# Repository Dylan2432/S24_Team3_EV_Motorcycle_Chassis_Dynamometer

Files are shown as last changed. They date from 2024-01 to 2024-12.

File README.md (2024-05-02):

# Electric Motorcycle Test Station

## Executive Summary

Proton Power is developing a cutting-edge battery to revolutionize electric motorcycles, addressing challenges in charging and range. Our team's project is to integrate a data acquisition system (DAQ) into a chassis dynamometer for crucial testing, ensuring accurate data collection and product validation. By selecting and integrating sensors meticulously, we aim to deliver a motorcycle test station with optimal performance while adhering to safety standards and engineering ethics.

## Capabilities

This dynamometer is designed to test and measure the performance metrics of an electric motorcycle. It shall have the following capabilities:
1. Fully remote-operable from PC 
2. Plot bike speed and torque in real time on PC
3. Data logging for later analysis
4. Support bike speeds of 0-75km/hr
5. Support incline testing for 0-8% road grade
6. Adjust bike speed in 1km/hr increments
8. Able to be disassembled for transport
9. Emergency stop capable

## Salient Outcomes

To be updated as the project progresses

## Project Demonstration & Images

Project demos and images will be uploaded as the project progresses.

## About Us

### Team

**Ethan Griffith** is a senior Electrical Engineering major at Tennessee Technological University with a minor in Mathematics. Ethan has an interest in wireless power transfer and mechatronics. For this project, Ethan focused on the design of the remote throttle control system. 

**Andrew Copeland** is a senior Electrical Engineering major at Tennessee Tech. His interests include power systems, control systems, and mechatronics. Andrew's role in this project is the design and implementation of a user interface for the test system.

**Aaron Littleton** is a senior Electrical Engineering major at Tennessee Tech with a minor in Mathematics. Aaron's interests include power systems and power grid design.  His role in this project is the design and implementation of the data acquisition system.   

**Dylan Scruggs** is a senior Electrical Engineering major at Tennessee Tech. Dylan has interests in power systems and mechatronics. His role in this project is the design and implementation of the controlled braking system.

**Jonathan Haas** is a senior majoring in Electrical Engineering and Business Management. Jonathan's interests are in critical power systems and power management. His role in this project is the design, implementation, and testing of sensors for the dynamometer.

**Branson Stephens** is a senior Elecitrical Engineering major at Tennessee Tech. Branson's interests are in PLC programming and Telecommunications. His role in the project is the design and implementation of a variable power supply to support the braking system that is controlled from the user interface.

### Faculty Supervisor

**Jesse Roberts**, M.S. is a lecturer at Tennessee Technological University. He received both his Bachelor's and Master's in Electrical Engineering at Tennessee Technological University. He is currently pursuing a Doctorate of Philosophy in Computer Science at Vanderbilt University.

### Stakeholders

The main stakeholder in this project is our customer Proton Power. Proton Power is a pioneering force in the realm of efficient energy, striving to overcome the global challenge of diverse charging requirements. Their cutting-edge battery technology promises faster charging and extended range, that will revolutionize the EV landscape. Proton Power is leading the design of an EV motorcycle battery with an impressive range of 400km on a single charge, offered at a fraction of the cost compared to existing models. We plan to aid them in this mission but providing data that will allow them to innovate their technology even further.

Another stakeholder in the project is Bob. Bob is a leading manufacturer specializing in electric vehicles (EVs), particularly focusing on providing affordable transportation solutions for third-world countries. With a mission to address the financial burdens associated with traditional gas-driven motorcycles, Bob has shifted its focus to producing EV bikes with lower maintenance and fuel costs. With the addition of the advanced battery from Proton along with the testing done by this team, Bob can greatly improve upon this mission.

### Recognitions

We would like to thank Jesse Roberts for continually giving feedback and advice on the project and investing plenty of time and effort into the project. We would also like to thank our mechanical engineering partnering team for providing useful insight from a unique perspective and helping the team with any mechanical problems. Next, we would like to thank past Capstone teams for their advice and support. Last but not least, we would like to thank Proton Power for giving us the opportunity to apply the knowledge learned in class to the bike they have provided us to test on.  

## Repo Organization

### [Reports](/Reports)

In the reports section of this repository information about the individual expectations for the reports and how they should be housed is provided.

The [**Project Proposal**](./Reports/Project%20Proposal/Project_Proposal_V2.pdf): Is the intial document that defines the problem and the goals of the project.

The [**Conceptual Design**](./Reports/Conceptual%20Design/Conceptual%20Design%20and%20Planning.pdf): Gives a deeper breakdown of what the problem is, a breakdown of the subsystems of the project, and a projected timeline and budget of the project.  

### [Documentation](/Documentation)

Contains:

[**Meeting Minutes**](/Documentation/Meeting%20Minutes) : typed meeting minutes from team meetings which occured weekly at the minimum

[**Signoffs**](/Documentation/Signoffs): reports for each approved subsystem containing functionality, constraints, schematics, analysis, and BOM

### [Software](./Software)

All software utilized for the project can be found in the this folder.

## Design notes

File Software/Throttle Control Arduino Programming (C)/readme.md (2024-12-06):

Must have Arduino IDE downloaded in order to open file

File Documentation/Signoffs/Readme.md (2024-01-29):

## How to submit a signoff or update a signoff:

### Submitting Signoff
1. Create the signoff markdown file 
2. At the bottom of the page select "create a new branch for this commit and start a pull request"
3. Submit the changes 
4. Name the pull request branch "name-signoff-subsystem name"
5. The comment should be "requesting signoff for name of subsystem"
6. Submit the pull request
7. Wait for faculty supervisor feedback on the pull request

### Updating Signoff

1. Edit the signoff markdown file 
2. Add a description of how you have addressed the feedback from the faculty supervisor
3. At the bottom of the page select "commit directly to"
4. Submit the changes 

# Required sections

Each signoff markdown file must contain the following sections and information:

## Function of the Subsystem

You must explain clearly what role the subsystem will play in the first section. This should clearly explain what the system is expected to do (ie. its atomic purpose from the conceptual design).

## Constraints

The second section should contain the constraints for the subsystem. The reasoning behind the constraints must be given. As a few examples, constraints may exist due to physics based limitations or requirements, other subsystem requirements, standards, ethics, or socioeconomic reasons. 

Each subsystem must have at least one constraint arising from standards, ethics, or socioeconomic well being.

## Buildable schematic 

The third section should show the buildable schematic directly embedded in the markdown file as a jpeg image. If the schematic is not clearly readable and appropriately sized, the supervisor will reject the signoff. 

The schematic must be appropriate to the design. ie. 3d model for a physical system or wiring schematic for a circuit. Further, the schematic(s) must contain every detail necessary for the design to be built by someone who has no knowledge of the design. Every relevant component value and measurement must be given.

The actual design artifacts (3d model, Cad files, gerber files, etc) must be uploaded to the documentation folder in the appropriate location.

## Analysis

A complete and relevant analysis of the design showing that it **should** meet the constraints and perform the desired function must be given. This analysis must be comprehensive and well explained so that it is convincing to the faculty supervisor. If the signoff request is not convincing either because the requirements and constraints are insufficient, unjustified, or not appropriately shown to be met by the design, then approval will not be given. Without approval, the components for the subsystem aren't allowed to be ordered. 

## BOM

A complete list of all components needed for the design must be given with the cost of each component and the total cost of the subsystem. The BOM should be a markdown table.

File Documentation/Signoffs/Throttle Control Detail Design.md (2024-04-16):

# Throttle Control Subsystem

## Functionality
The purpose of the Remote Throttle Control Subsystem is to be able to adjust the speed of the EV bike while it is on the dyno without having to be near the bike and adjust it manually. It allows the adjustments of the speed to be made based on the input of the user and be able to set test runs to change to multiple speeds within a single test run. This is done for safety concerns so that there does not have to be a user on the bike while it is running on the dyno and instead can be operated from a safe distance.

## Constraints
| No. | Constraints | Origin |
|-----|---|---|
| 1 | Be able to rotate the entire range of the throttle on the bike by a signal from a controller. | Safety Constraint |
| 2 | Support repeatedly testing the bike from 0 km/h to 50 km/h and then back down to 0 km/h. | Design Constraint |
| 3 | Be able to adjust operating speeds in 1 km/h increments and measure response time. | Design Constraint |
| 4 | Be able to adjust the throttle from a dead stop to a full throttle in under 200ms. | Design Constraint |

1. This constraint is set into place to keep all personnel operating the equipment and testing the bike safe. By allowing it to be operated remotely, all testing can be done at a safe distance, so no one will be injured in case something were to go wrong. It also serves as a way to increase the accuracy of testing by not having to worry about the weight of someone on the bike while it is running and being able to precisely change the speed at desired increments. 

2. This is a specification that was made by the customer. According to this, test runs must be incorporated into the programming for the user interface so that the user can create set runs to allow the bike to go through without having to change it every time. For example, the user should be able to select a test run through the user interface that will make the bike go from 0 km/h to 50 km/h and then back to 0 km/h, and the bike will perform this run without having to manually enter in each step every time. This will make the testing procedures much more convenient for tests that need to be repeated.   

3. This is an extremely important constraint that was requested by the customer because it specifies how accurate the throttle control system needs to be. This also provides evidence for why a remote throttle control system is needed because precisely incrementing the speed by 1 km/h manually with someone on the bike is difficult to achieve and can be inaccurate. This constraint affects the design of the system because in order to achieve this, a motor must be used that can be accurately controlled enough to make these small adjustments to the throttle handle.

4. This constraint is to ensure that the throttle control system will be able to accelerate fast enough by making the throttle able to rotate a dead stop to full throttle faster than a person can. To determine this constraint 10 different test runs were timed to see how fast a throttle handle can be rotated, and the average of these runs was taken to determine that this can be achieved in 200ms. 

## Schematics



### Figure 1 – Throttle Control Assembly
The first schematic shown in the figure is an overview of the system as a whole. It shows exactly how a clamp will be used in conjunction with a motor to control the throttle of the bike. It is important to note that without having access to the Bob bike yet or a 3D model of it, a generic throttle handle was used for the diagram. However, with the subsystem that has been designed, it will not only work with the Bob bike but will also be compatible with any other bike used.  This system can be broken down into four different parts: The clamp, motor, driver, and microcontroller. 
The first part is the clamp. This has been custom-made not only to fit the motor being used but also to be fitted to a motorcycle's throttle handle. This system will be 3D printed to make it more cost-efficient and provide the desired results for this specific outcome. 



### Figure 2 – Clamp
The motor that will attach to this clamp is a Nema 17 motor. A full explanation as to why this specific motor was chosen can be found in the analysis section. To connect the microcontroller to the motor, a driver must be utilized. For this system, an A4988 driver will be used to control the motor with a 24V DC power supply to power the motor. The wiring to connect these components can be found in Figure 3 below. 



### Figure 3 – Full Wiring Diagram
In the middle of the diagram, you can see that the A4988 driver is connected to the motor through 4 pins on the right of it and the motor is powered by the 24V DC power supply connected to the two pins in the top right corner. A Decoupling capacitor will be added to protect the chip and motor from any voltage spikes. The bottom right corner is connected to the Arduino and this supplies power to the logic pins. The two pins in the bottom left corner are what control the motor, and these will connect to the output pins on the Arduino. The two pins above that are connected are the sleep and reset pins which need to be connected for the driver to run. Finally, the top left corner will have MS1 set to high to convert the motor from 200 steps/rev to 400 steps/rev, the reasoning behind this will be explained further in the analysis.

## Analysis
The goal of this subsystem is to create a way to remotely control the throttle of an EV bike while it is running on a dyno. The solution that has been created will accomplish this using four main components: microcontroller, driver, motor, and clamp. With these components, the throttle can be controlled by the user simply with just programming in the microcontroller. This will comply with all the constraints given and accomplish the results desired by the customer. First, a full explanation of each component and how it will all work together must be given.

The microcontroller lies at the core of all of this. It is used because this is the most efficient way to take an input signal from something and run preset calculations to determine what will be sent to the motor. The same microcontroller that is being used to gather the input RPM from the bike, ATMega 2560 Board, will be used to send the instructions to the motor. This reduces any time delays or confusion by communication between two microcontrollers by doing all of it on a single one. However, the microcontroller cannot efficiently communicate directly with the motor and will need a device to fix this problem.

The driver is the middleman between the microcontroller and the motor. It takes input from the microcontroller and sends it to the motor. The driver also takes the power of the power supply and sends it to the motor. The A4988 has a current limiter that can adjust the current going to the pins of the motor by simply adjusting the screw in the bottom middle of the driver. This will ensure that the motor is operating under safe currents and won’t be damaged. However, the driver has other equally important roles. 

The A4988 driver has an extremely useful feature that will be utilized in this project and that is microstepping. This will allow the motor to have finer movement control compared to the base setting. By setting the MS1 to high it will put the driver in half-step mode which essentially doubles the number of steps a motor can take in a full revolution. This will be useful in this project because most throttle handles only rotate around 90 degrees so in the base setting for the motor of 200 steps/rev, or 1.8 degrees/step, only gives you 50 steps to control the throttle with. Considering the bike can reach top speeds of over 80 km/h and the throttle needs to be controlled in 1 km/h increments, according to constraint 3, more steps will be needed to precisely control the throttle. Putting the throttle in half-step mode changes the steps/rev to 400 and will allow the throttle to be controlled at the desired level of precision.  

The motor is going to be the muscle behind turning the throttle handle. It gets the instructions from the microcontroller and the driver does exactly what they instruct it to do. The most important aspect of the motor is making sure that it is light and can be easily mounted. However, other factors must also be considered like being controlled with enough precision to make small adjustments in the throttle, strong enough to rotate it, and fast enough to meet the constraints. The Nema 17 stepper motor being used weighs less than a pound so mounting weight won’t be an issue and it works perfectly with both the driver and microcontroller. Luckily since throttles need to be easily turned by humans using just their wrists, the motor does not need to be able to supply that much force. Nema 17 motors also have an extremely high RPM even from a dead stop. To determine how fast the motor can reach the 90-degree mark from a dead stop, tests were run timing the motor to determine the exact time. After running numerous tests filming the motor in 960fps next to a timer it was determined that it can reach the 90-degree mark in 70ms which is over 4 times as fast as the duration in the constraint. The only issue with the motor is getting the throttle handle to rotate as the motor spindle rotates.

This is where the clamp comes in. The clamp needs to be able to attach the motor to the throttle so that as the motor turns the throttle handle will also turn. It was determined that the most efficient way to do this is by 3D printing a custom clamp. That way it is both affordable and works perfectly for the application it is being used for. The design that was made in Figure 2 is similar to a double C-clamp. The reason for this is so that the motor spindle can be perfectly in line with the throttle handle and the degrees of rotation won’t be thrown off once it is tightened down. It is made so that it be easily connected and removed simply by just unscrewing it. Also, the ends of each screw are in a V-shape so that it will conform to the throttle handle by creating two points of contact on each end. There will be added foam pads on each of the clamps to create more friction between the clamp and the handle and keep it from sliding. These ends will also be screwed on so that the screws can be removed from the clamp if needed and fine adjustments can be made so that curved ends won’t get in the way of tightening the clamp down. A safety measure that will be implemented is adding silicon tape to the throttle to protect the handle from any possible damage from the clamp and adding extra friction to ensure the clamp doesn’t slide at all when being rotated. 

With this setup, the throttle handle of the bike can now be completely remotely controlled by the user. The only other part is programming inside the microcontroller to adjust the speed of the bike as needed. This will depend on several factors on the bike including the max degrees of rotation on the throttle handle, the change in RPM per degree of rotation, and the max RPM of the bike, so it will need to be tested once the bike can be set up. This will also be in conjunction with the user interface subsystem to connect what the user inputs and output instructions to the motor. The last part is mounting the motor to the end of the throttle handle but since this mount will likely attach to whatever dyno the Mechanical Engineering team decides to use it will have to be chosen based on their selection. 

## BOM (Bill of Materials)
| Item | Item # | Quantity | Price | Total  |
|---|---|---|---|---|
| Stepper Motor Nema 17 Bipolar 40mm 64oz.in(45Ncm) 2A 4 Lead | 17HS16-2004S | 1 | $12.99| $12.99 |
| A4988 Stepper Motor Drive with Heat Sink for Arduino | MG046 | 1 | $6.99 | $6.99  |
| EMITEVER 24V DC Power Supply, 96W, 120V AC to 24V DC Converter 4amp | EM-DC-96W | 1 | $29.99| $29.99 |
| 2 Rolls 1IN X 10FT Grip Tape, Rubber Tape, Silicone Tape, Grip Tape for Handles | MB-YCJ-0131 | 1 | $11.99 | $11.99 |
| Foam Tape Strong Pad Mounting, Black Self-Adhesive Tape	 | AV001	 | 1  | $5.99 |	$5.99 |
| **Subsystem Total** | | | | $67.95 |

## References
- HowToMechatronics. (08/2023). Arduino Stepper Motors - The Ultimate Guide. Retrieved from [https://howtomechatronics.com/tutorials/arduino/stepper-motors-and-arduino-the-ultimate-guide/](https://howtomechatronics.com/tutorials/arduino/stepper-motors-and-arduino-the-ultimate-guide/) [Accessed on 3/30/2024]

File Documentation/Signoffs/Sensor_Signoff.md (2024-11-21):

# Sensor Signoff
## Functionality

The functionality of sensor integration within an electric motorcycle dynamometer is essential for collecting data to accurately assess the motorcycle's performance. By seamlessly integrating sensors into the dynamometer and outputting gathered signals to the DAQ system, users can conduct comprehensive testing and optimization of the electric motorcycle.

## Constraints

|No. |Constraints |Origin |
|---|---|---|
|3|	The system shall support a roller with induced torque up to 19.13 lb-ft.	|Design Constraint|
|6|	Comply with NFPA NEC 310.16 Conductors for General Wiring and NEC 250.122 Equipment Grounding Conductor Sizing	|Ethics/Standard Constraint|
|16|	Sensors must output either digital or analog signals of 0-10V	|Constrains to DAQ|
|19|	Sensors must be able to measure within the range of expected bike values	|Design Constraint|
	
3:  This constraint requires the sensor integration system to support the drum’s maximum torque of 19.13 lb-ft. Including a 20% safety factor, the system must be able to measure up to 22.96 lb-ft. It also requires supporting the drum’s maximum RPM of 1,288.

6:  Each sensor will contain wiring to communicate with the DAQ. This wiring must meet the codes listed to ensure safety and correct operation.

16:  This constraint is set and satisfied by the DAQ subsystem, which has ports that can supply or receive 0-10 volts.

19:  Due to the electric motorcycle’s data sheets, it has been calculated that the test data must be able to be captured in these ranges:

RPM:  0-1,288 RPM

Torque:  0-25.94Nm (calculated using 22.96 lb-ft with a conversion ratio of 1lb-ft = 1.3558 Nm)

## Schematics

### Rotary Torque Sensor Application:

 

The image above shows where the rotary torque sensor shall be installed within the dynamometer's mechanical system. It shall be coupled directly between the drum (labeled Load Equipment) and one of two electric motors (labeled Power Equipment). The sensor shaft has a coupling on each side that connects the solid protruding shaft of the sensor. Then, the sensor can measure the RPM seen by an internal encoder and the torque applied by an integral strain gauge attached to the solid protruding shaft.

### Rotary Torque Sensor Wiring Schedule:
 
 

The image above shows the wiring schedule for the torque sensor cable. The connections are to the DAQ (NI USB_6215) and a USB to RS485 converter. This allows the user to program the sensor's parameters and provides a redundant data display to ensure the DAQ output matches the sensor's output. The ninth pin is connected to the cable shield, which will be attached to terminal 11 on the DAQ to eliminate any chance of noise generated onto the signal from electromagnetic interference.

### Rotary Torque Sensor Installation Dimensions:



The image above shows the required dimensions in millimeters for mounting the sensor into the dynamometer.

## Analysis
### Rotary Torque Sensor:
The torque sensor is a transducer that converts mechanical torque into an electric output signal. This is achieved by attaching strain gauges to the shaft. As the shaft's torsion increases, the strain gauges' value proportionally changes, and the change in voltage or resistance measured is used to calculate the shaft's induced torque. The drum’s maximum torque from the bike’s 3500 W drive motor is 19.13 lb-ft. With a 20% safety factor, the system must then be able to measure up to 22.96 lb-ft. The selected sensor can support up to 100 Nm, which converts to 73.756 lb-ft, exceeding any anticipated torque capacity from the drum.

### RPM Sensor:
The rpm sensor is internally incorporated into the selected component. The RPM is measured with an encoder that reads the rotations per minute of the shaft passing through the device. To calculate the drum’s maximum RPM, we multiply the gear ratio by the bike’s maximum RPM. To calculate the gear ratio, we use the diameter of the bike’s rear tire, which is 22 inches, divided by the diameter of the drum, which is 12 inches. The gear ratio equals 1.833. The bike’s maximum RPM is calculated using RPM=[(Top Speed)(60)]/[(π)(Tire Diameter)]. The bike’s top speed is 74 kmh or 20.56 m/s, and the rear tire diameter is 22 inches or 0.559 m. Therefore, the bike’s maximum RPM equals 702.45. Then, we multiply the gear ratio by the bike’s maximum RPM of 702.45, giving us the drum’s maximum RPM of 1,288. The selected sensor is rated for up to 10,000 RPM and will support up to 15,000 RPM, which is well above the drum's anticipated RPM. The sensor will be powered by a 24-volt power supply and output a 0-5 volt signal. After calculating the gearing ratio and implementing that into the DAQ software, the output signal can be converted to display the correct RPM of the bike being tested on the dynamometer.

### Standards:
To meet the wire sizing standard discussed in the constraints, the team will verify that the wiring included with the sensors is at least 24 AWG. This is the recommended wire size for 0-5 volt sensors to meet NEC codes. 

## BOM

|Manufactuer			|Item					|Part No.	|Quantity	|Price|
|ATO Industrial Automation	|ATO Rotary Torque Sensor 100Nm, +5V	|ATO-TQS-D03|	1|		$1,021.99| 
|ATO Industrial Automation	|ATO USB to RS485 adapter PLUS Software	|ATO-UT-890A|	1|		$335.00|
|Subsystem Total| 	 	 	 	|$1,356.99| 

## References

Torque Sensor: https://www.ato.com/rotary-torque-sensor-10000-nm

USB to RS485 adapter: https://www.ato.com/usb-to-rs485-converter

NU USB-6215 Specs: https://www.ni.com/docs/en-US/bundle/usb-6215-specs/page/specs.html

NU USB-6215 Pinout: https://documentation.help/NI-DAQmx-de/6215Pinout.html

How rotary torque sensors work: https://www.futek.com/torque-meter

Understanding cable shielding: https://www.mouser.com/pdfdocs/alphawire-Understanding-Shielded-Cable.pdf

Adapter wiring diagram: https://az849230.vo.msecnd.net/resources/ic832a_rev3_20242.pdf

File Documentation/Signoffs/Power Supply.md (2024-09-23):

## Functionality ##
This subsystem is to supply the current to the motor windings for DC injection braking used in the braking subsystem. The user will be able to change the amount of current that is entered into the motor winding. It will have a power supply going into a buck converter and the current will change depending on the duty cycle of the MOSFET which is used as a switch. The user will set the duty cycle, this will cause the current to increase as the duty cycle decreases and to decrease as the duty cycle increases.

## Constraints ##
| No. | Constraints | Origin |
|-----|---|---|
| 1 | Current entering the motor winding must not exceed 18.4375 amps | Design Constraint |
| 2 | Must be controlled from the user interface | Design Constraint |
| 3 | Inductors, diodes, and MOSFETs must be able to withstand a current of 16.867A | Derived from further considerations|
| 4 | Comply with all relevant codes and standards listed in II. Ethical, Professional, and Standard Considerations. | Safey Constraint|

1. This value is based off adding 150% of 125% of the FLA of the motor of 5.9. There is risk of damanging the motor if this value is exceeded.
2. It must be able change the voltage or current from the user interface. This will increase safety as the user is further away from high amperage of the buck converter.
3. This is the max amount of current that will go through the inductor, diode, and MOSFET. This value wil be further disccussed in the analysis portion.
4. One example that must be folowed is NEC 310-16 ampacity chart to ensure proper wiring for the amount of current in the circuit

## Schematics ##

Above: Kicad Schematic


Above: Arduino Nano pinout, PWM pins have the ~ symbol.

Above: Arduino Nano Screw Terminal board

## Analysis ##
The basic operation of a buck converter is when the switch is closed the inductor is charged and no current flows through the diode. Then the switch is opened and the inductor acts as the source and goes through a loop through the diode until the switch is closed again.



Above: Basic Topology of Buck Converte

The equations used to determine componet sizes are from Texas instruments.[1]
We have a 48V, 2.2A source which we want to convert to a 14.667A output to enter in the motor winding. The duty cycle to acclompish this can be found from the following equation.



Where we will assume our efficieny, n, is 0.9 which Texas Instruments says is not unrealistic for a worst-case efficiency.
If Vout is 7.2V, Vin is 48V, and efficiency is 0.9 we have duty cycle of 16.667%. From conservation of energy Pin = Pout and since the input power is known and output voltage is known we can calcutlate the output current is 14.667A. This value will not be the same in reality due to losses but it will be close to accurate.

Then we will calculate the miniumum inductor value from the following equation.



The delta I_L, which is the inductor ripple current, can be estimated to 30% of the output current and using a frequency of 62.5kHz we arrive at a minimum inductance value of 22.25 microhenry. We used a 33 microhenry inductor which is above the minimum value calculated.

To determine the maximum current that will flow through our inductor, diode, and MOSFET we will use the following equation.



This gives us a value of 16.867A and the componets must be sized to handle this current and the componets chosen will be atleast 10% above this value.

To determine minimum output capacitor size the following equation is used.



Allowing for the voltage ripple to be 100mV the minimum capacitor size is 88 microfarad. As the output capacitor size increases the amount of voltage ripple will decrease.

To determine the minimum input capacitor size the following equation is used. [2]



Having the input votlage ripple to be 100mV we have minimum input capacitor size of 135.8 microfarad.

To assist with power dissipation in the diodes two Schtokky diodes in paralle were used. The forward voltage is 0.87 which causes the power dissipation to be (16.871/2)*(0.87) = 7.34W.

The arduino nano was chosen as it allows for 5V, 8 bit PWM on each PWM pin. Since the clock is 16Mhz, an 8 bit PWM resolution allows for a frequency of 62.5kHz. The 8 bit PWM allows for a duty cycle resolution 0.4% which will allow for greater control.

To simulate the circuit LTSPICE was used.


At 50% duty cycle, the expected current value would be 4.4A. The measured value in LTSPICE was 4.38A

At 75% duty cycle the expected current value would be 2.93A. The measure value was 2.94A.

The current values were within 5% of error from a duty cycle of 15% to a duty cycle of 95%. Which allows for a current range of 2.32A - 14.34A.
If we do not want any current applied we can set the duty cycle to 0 as the MOSFET acting as a switch will never close.

### Arduino and User Interface ###
The MOSFET will be switched on and off from PWM of an Arduino Nano with a frequency of 62.5 kHz and a PWM resolution of 8 bits which gives us 256 levels. This allows us to adjust the duty cycle in 0.391% increments.

The user will enter their desired output current at the user interface. This will correlate to a analog voltage output going to the Arduino Nano as an analog input, that input will then set the duty cycle that is outputed to the MOSFET.

The PWM resolution is 8 bits while the pins have 10 bits of resolution when using analogRead() on pins A0-A7.

### PCB Layout and Thermal Considerations ###
Below is some general points for PCB layouts for a Buck Converter from ROHM semiconductor [3]




Above: PCB layout for buck converter

Altium has a current table to PCB trace width table that says what trace width will limit your temperature rise to 10 °C with 1 oz./sq. ft. copper weight.[4] For the diodes the max amount of current going through one of them would be 8.4335A so a trace width of 260 mils(0.26 inches) or higher would be chosen. Near the indcutor and diodes where there is a larger current and more power dissipation there is larger traces to assit with this problem. We also have thermal vias near diode, inductor, and the MOSFET to help with heat issues.

Below is PCB thermal layout tips for DC/DC converters from texas instruments.



We will not have a package with DAP. What Texas instruments means by the "pizza" concept is the fact that the heat will go out radially and you want to avoid cuts closer to the device. They provide an image of two layouts and the heat flow between the two to show this concept.



We will also place the higher current componets such as the inductor, MOSFET, and diode closer towards the center so there is more area for the heat to spread out radially. However they cannot be too close as too avoid the heat adding together to create a much greater temperature rise.

## BOM (Bill of Materials) ##
| Item | Manufacturer | Quantity | Price | Total  | Link|
|---|---|---|---|---|----|
|TXN 100-148 Power Supply | TRACO Power |  2 | $25.03 | $50.06| https://www.mouser.com/ProductDetail/TRACO-Power/TXN-100-148?qs=iLKYxzqNS776y9pVP5bizw%3D%3D |
|Screw Terminal Block Breakout Module Board for Arduino Nano/Micro  | CZH-LABS | 1|$22.00 |$22.00| https://www.amazon.com/CZH-LABS-Terminal-Breakout-Module-Arduino/dp/B07QMRDZ3W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  |
|Arduino Nano | Arduino| 1 | $25.10| $25.10| https://www.amazon.com/Arduino-A000005-ARDUINO-Nano/dp/B0097AU5OU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|
|Arduino Nano USB cable| --- |1 | 6.99| 6.99| https://www.amazon.com/DIYables-Mini-Cable-Arduino-Pieces/dp/B0C7BMS5FG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|
|Inductor 74437529203330 |  Wurth Elektronik | 2 | $9.43 | $18.86|https://www.mouser.com/ProductDetail/Wurth-Elektronik/74437529203330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 | 
|Output Capacitor MAL212029101E3 | EPCOS / TDK | 2 | $5.41 | $10.82| https://www.mouser.com/ProductDetail/EPCOS-TDK/B41858C9227M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 |  
|Input Capacitor B41858C9227M | EPCOS / TDK | 2 | $1.90 | $3.80| https://www.mouser.com/ProductDetail/EPCOS-TDK/B41858C9227M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 |
|Schottky Diode RB218NS100TL | ROHM Semiconductor | 4 | $2.09 | $8.36| https://www.mouser.com/ProductDetail/ROHM-Semiconductor/RB218NS100TL?qs=4v%252BiZTmLVHGSz1dy1RhSpg%3D%3D|
|MOSFET SQJ872EP-T1_GE3 | Vishay / Siliconix | 2 | $1.46 | $2.92| https://www.mouser.com/ProductDetail/Vishay-Siliconix/SQJ872EP-T1_GE3?qs=y6ZabgHbY%252ByhIql41nGYsQ%3D%3D |
|30ft 14AWG wire | NAOEVO | 1 | $29.99 | $29.99| https://www.amazon.com/dp/B0C27C1RCX/ref=twister_B0CB468CZK?_encoding=UTF8&th=1 |
| **Subsystem Total** | | | | $178.90|

## References ##
[1]https://www.ti.com/lit/an/slva477b/slva477b.pdf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
[2]https://www.ti.com/lit/an/slyt670/slyt670.pdf
[3]https://fscdn.rohm.com/en/products/databook/applinote/ic/power/switching_regulator/converter_pcb_layout_appli-e.pdf
[4]https://resources.altium.com/p/pcb-trace-width-vs-current-table-high-voltage-design
https://www.mouser.com/pdfdocs/buckconverterdesignnote.pdf
https://docs.arduino.cc/hardware/nano
https://www.arduino.cc/reference/en/language/functions/analog-io/analogread/
https://www.ti.com/lit/ds/symlink/tps40200.pdf

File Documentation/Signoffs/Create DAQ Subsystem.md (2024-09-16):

# DAQ Signoff

## Functionality

The primary function of the data acquisition (DAQ) is capturing and displaying relevant testing data in real-time. The DAQ resolves this constraint through a process containing signal conditioners, signal converters, a controller, and software. Through the execution of correctly applying these systems, accurate, real-time data will be derived to support the generation of a model.

## Constraints
|No. |Constraints |Origin |
|---|---|---|
|3|The DAQ must have at least 2 analog inputs, to cover all possible sensors being used from the sensor integration system. |Design Constraint |
|16|Analog input pins must be able to read an output of 0-5 V or 0-10 V input from the sensors. |Derived from further considerations|
|17|The DAQ must have an analog-to-digital converter with a minimum of 10-bit resolution. |Derived from further considerations|
|18|The DAQ must have a sampling rate of at least 4.8kS/s |Derived from further considerations|
|19|The DAQ must be able to read the RPM sensor in increments of 1 rpm and torque in incremets of 0.1 N-m. |Derived from further considerations|

3.) To make sure all possible sensors are accounted for, it is vital to have a minimum of 2 analog inputs.

16.) An industry standard for sending a signal from a sensor to a data acquisition system or controller is a 4-20 mA current loop or 0-5v voltage.  Because of this, the daq selected must be able to read in either 0-5v or 0-10v sensors on an analog input pin.

17.)  Using the resolution equation in the analysis, a 10-bit ADC would allow the team to meet the minimum specified resolution. 

18.) Based on different DAQ applications, it is vital that the DAQ system operates at a minimum of 4800S/s.

19.)  The values must be displayed with these increments to ensure that the values that are displayed are accurate enough.  These values are determined by the calculations for each of the sensors, along with the values that are given by the daq.

## Schematics

Note: Due to the braking subsystem, the sensors are subject to change. However, if changes in the braking subsystem occur, there are plenty of analog inputs available for added sensors. Adding additional power for sensors will be addressed based on specific sensors in the sensor integration subsystem.

### NI USB-6215 Wiring Diagram



## Analysis

### USB-6215:

The design of this subsystem presents a National Instruments USB-6215 multifunction DAQ device and LabVIEW software to effectively power sensors, capture sensor outputs, calibrate raw sensor data, perform necessary conversions/calculations, and send data to the user interface system for display/logging.  The USB-6215 has 16 analog input pins which exceeds the minimum requirement of 2 pins.  This satisfies constraint 3.  The analog input pins allow for interfacing with analog sensors to capture test data.  It also has 8 digital I/O pins, 4 PWM output pins, and 1 5V pin.  The PWM and digital I/O pins allow for the addition of digital sensors or motors from other subsystems.  This system allows analog input of ±0-10 volts which widens the variety of available sensors, compared to only 0-5v. The system itself will be powered by the USB-B connection. The system communicates with a laptop/PC via the same USB-B connection, where it will send the measured data to the user-interface system. 

  The system will operate with the LabVIEW software, making it easy to work with sensors, motors, and displays.  This is also where the raw sensor data will be converted to relevant metrics, to then be sent to the user interface for display.

### Resolution and Sample Rate:

To prove that the NI USB-6215 system can successfully sample accurately enough for all of the sensors, the team finds values to determine if this specific system is fast enough to determine real-time values. Finding the maximum values of sample rate and I/O pin currents, as well as the resolution, can show how accurate and precise the sensors are measuring.

The sample rate is given in the data sheet of the system as 250kS/s, which exceeds constraint 18 by a significant amount.  This is very high compared to most systems and allows the system to capture measurements at a greater accuracy, along with a better resolution.

Use the following equation to determine the precision that the USB-6215 provides at 16 bits of resolution: 



  Where VD is the full-scale input range of the logger, which is 10 V, VS is the full-scale range of the measured signal, which is 10 V, E is the engineering units that represent VS, Resolution represents the smallest change the DAQ can measure, and B is 0 as the logger is unipolar meaning it will measure from 0-10 V.

We can verify the accuracy of the equation through an example. Say we have a DAQ with an input range of 0-10 volts, a sensor that measures current from 0-100 amps with an output range of 0-10 volts, the sensor was unipolar and the DAQ has a bit resolution of 10 bits. 10 bits represent 1024 locations that can be addressed. In this example our resolution is 0.09765625 A/location which is the smallest change the DAQ can measure. Then if we multiply our resolution by the number of locations the DAQ can provide, 1024, we get back to 100 A.

  Our E value was chosen as higher than the expected value to prepare for a worst-case scenario. A lower E value would lead to more precision.

  For RPM, our E is 1500 RPM, this is based on the max RPM of the drum being 1,288 RPM. This means the precision is 0.01137. 1% of E is 15; therefore precision of 0.01137 meets and exceeds the limitations of constraint 19.

  For torque our E is 50 Nm, this is based on the max torque of the drive motor being 25.94 lb-ft, which translates to 35.17 Nm. This means the precision is 0.01388 Nm. 1% of E is 0.5; therefore precision of 0.01388 meets and exceeds the limitations of constraint 19.

  These values are more precise than other dynos on the market, which provides confidence in the ability of the USB-6215 to work as a DAQ.

### Range:
The USB-6215 brings in 0-10 volts (10.4 volts max) through the analog input ports, which meets constraint 16 for analog inputs. It cannot use 4-20 mA as input, however, with an external 4-20mA to 0-10v converter circuit, the system could be compatible with 4-20mA sensors.  This is an ideal situation due to the less noise these signals produce compared to 0-10V.  This is discussed in the sensor implementation subsystem, if necessary.

## BOM
|Item |Quantity |Price |Total |
|---|---|---|---|
|NI USB-6215 DAQ|1 |\$ 1903.00 |$ 1903.00|
Subsystem Total |||$ 1903.00|

## References

USB-6215 Data sheet:
USB-6215 Specifications - NI

USB-6215 Information:
 USB-6215 - NI

Bit resolution requirement
https://www.dataq.com/resources/pdfs/article_pdfs/adc-resolution.pdf

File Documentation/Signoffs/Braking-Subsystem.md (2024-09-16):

# Brake Control System

## Functionality
 &nbsp;&nbsp;&nbsp;&nbsp;&nbsp; The Brake Control System is being implemented to allow for the ability to apply a user-controlled load. This system will be the driving factor behind ensuring the customer’s desires are satisfied. With this system the user shall be able to induce a controlled load on the drum’s shaft in order to derive a torque measurement as well as apply a braking resistance. This will be made possible with the implementation of a 3-phase induction motor connected to the drum shaft mechanically. In addition, a Variable Frequency Drive (VFD) will be connected to the motor with a braking resistor connected to the VFD. Through the coaction of these components, this subsystem will be able to deliver desired metrics over various simulated conditions.

## Constraints
|No. |Constraints |Origin |
|---|---|---|
|3|The system shall be able to handle a roller induced torque of up to 19.13 lb-ft. |Design Constraint |
|5|Comply with all relevant codes and standards listed in II. Ethical, Professional, and Standard Considerations focusing on NFPA 79 – 10.7.1. (emergency stops) |Safety Constraint|
|20|The motor shall have a maximum torque rating of, at minimum, +20% of maximum expected torque reading. |Derived from further considerations |
|21|The motor shall be able to handle a maximum expected roller rotational speed of 1288 rpm. |Derived from further considerations|
|22|The VFD must be rated for a 460 volt, 1-phase input. |Derived from further considerations|
|23|The VFD must be rated for a normal load current rating of 10.96 amps. |Derived from further considerations|
|24|The braking resistor shall be capable of dissipating, at minimum, 3500 Watts. |Derived from further considerations|

3.) The maximum calculated torque value that the applied motor shall experience from the roller is 19.13 lb-ft. The selected motor must be able to safely and effectively handle all events in which values up to this maximum are present. Therefore, the process of motor selection will include major attention to the breakdown torque capacity.<br><br>
5.) This system will follow all relevant codes and standards listed in the conceptual design and proposal. One standard with a high magnitude of importance that will be met throughout this design is NFPA 79 – 10.7.1. This standard encompasses that any electrically operated industrial device must possess an emergency stop. This will be implemented through the collaboration of both this system as well as mechanical design.<br><br>
20.) To ensure safety and the selected motor’s ability to handle to maximum expected torque value, the maximum applied torque with an extra 20% must be within the component’s torque range. This comes out to a maximum torque of 22.96 lb-ft. This value will be used within the torque evaluation to determine the most suitable motor.<br><br>
21.) To correctly operate and ensure component safety, the selected motor must be able to handle rotational speeds up to 1288 rpm. This rating will be a driving factor in the selection of the implemented motor. If the motor selected can’t handle a 1288 rotational speed, stator damage may occur.<br><br>
22.) To ensure the selected VFD can operate within the voltage supply available, it must be rated for 460 volt, 1-phase input. This is due to 3-phase power not being readily available at the build site.<br><br>
23.) The calculated output current capacity needed to use the VFD as a phase converter is 10.96 amps. Therefore, the selected VFD must be rated for these conditions.<br><br>
24.) In order to ensure the selected braking resistor is sized correctly, it shall be rated to handle the bike’s maximum power output (3500 W).<br><br>

## Schematics
### Full Brake Control System Diagram


&nbsp;&nbsp;&nbsp;&nbsp;&nbsp;Presented above is the full system diagram of how components will be connected to create a correctly functioning regenerative braking system. The VFD will be fed a 1-phase, 460 V input through 2 if its input terminals (R and S). Through phase conversion, this will then be outputted to the 3-phase motor from its output terminals (U, V, and W). The drive’s ports for integrating a brake resistor (B1 and B2) will also be used to allow for power dissipation. Additionally, to control the drive’s operating functions, the analog input port will be fed signals from the DAQ. The operation and purpose of each of these components will be further explained in the analysis section as well as the support subsystems.
### Dayton 3-Phase 5 HP Motor Ratings


&nbsp;&nbsp;&nbsp;&nbsp;&nbsp;Presented above are the motor ratings of this selected 3-phase 5 Horsepower motor. These specifications meet all motor requirements needed to ensure correct and safe operation. The reasoning for this motor selection will be further explained in the analysis section.

### E-Stop Wire Diagram


&nbsp;&nbsp;&nbsp;&nbsp;&nbsp;Presented above is the wire diagram portraying how an emergency stop push button will be wired to the VFD. The purpose and application of this will be further explained in the analysis section.

## Analysis
### Motor Selection Analysis
&nbsp;&nbsp;&nbsp;&nbsp;&nbsp;The Dayton 5-HP 3-phase motor was the decided upon component to be used to drive the ability to create a controlled braking system. This component was selected through a series of well thought out steps and calculations.<br><br>

&nbsp;&nbsp;&nbsp;&nbsp;&nbsp;The first motor parameter that was looked at in this selection process was the motor duty rating. Due to using a VFD, an inverter duty motor rating was decided to be a requirement. This is due to these motors being able to run at much lower speeds without overheating and being capable of withstanding higher voltage spikes than non-inverter rated motors. Since this dyno will be testing the bike at various speeds and the max rotational speed that the motor will be driven at is lower than its rated speed, this is a crucial capability to ensure efficient and safe operation. <br><br>

&nbsp;&nbsp;&nbsp;&nbsp;&nbsp;After selecting the type of motor, the next characteristics that were looked at was the torque and rpm ratings needed to provide correct operation. Before these metrics could be calculated, a roller size had to be set. This metric was decided to be 12 inches in diameter based on safety calculations and considerations made by the mechanical team. With this parameter, the maximum rpm that the motor must be able to test can be found. This is derived using the equation $RPM = \frac{(Speedmax(\frac{m}{s}))(60)}{(π)(Diameter(m))}$.
This equation was pulled from the website emotorsdirect listed below in the references section. The maximum speed of the bike (74 km/h or 20.56 m/s) and the 12-inch diameter of the roller are the metrics used to compute the rpm value with the given equation. After plugging these values in, the maximum rotational speed of the roller comes out to 1288 rpm. This value sets a maximum rotational speed that the motor selected most be able to read. Moreover, the maximum torque of the roller is derived using the equation $Power = (torque)(2π)(RPM)$. This is the base equation pulled from the website powertestdyno, also listed in the references section, to derive the equation needed to find the maximum torque value. To get this equation, the relation between horsepower and torque (lb-ft) is used: $1 HP = 33,000(\frac{(lb-ft)}{min})$. Plugging this relation in gives the equation $33,000(\frac{(lb-ft)}{min}) = torque(lb-ft)(2π)(RPM)$. To then simplify this equation, each side can be divided by 2π to compute the equation $5252(\frac{(lb-ft)}{min}) = torque(lb-ft)(RPM)$. Then, by dividing each side by 5,252 the final needed equation comes out to $HP = \frac{(torque(lb-ft))(RPM)}{5252}$. This can then be rewritten as $torque(lb-ft) = \frac{(HP)(5252)}{RPM}$.  To find the maximum torque value with this equation, the max power rating of the bike (3500 W) is converted to horsepower with the relation 1HP = 746 W. This gives a horsepower value of 4.69. The then previously calculated 1288 rpm metric is plugged in to find that the max torque of the roller is 19.13 lb-ft (25.94 Nm). However, for safety and operation assurance, 20% is added to this value. This brings the max breakdown torque that the motor must handle up to 22.96 lb-ft. With these two values, the parameters at which the motor must operate were set.<br><br>

&nbsp;&nbsp;&nbsp;&nbsp;&nbsp;When comparing the required ratings with the selected motor’s datasheet, it can be seen that all requirements are met with considerable safety factors. For, the rated rotational speed and breakdown torque ratings of the motor are respectively 1760 rpm and 46.19 lb-ft. With these 2 ratings, the requirements in both constraints 3 and 21 are met. Furthermore, with a breakdown torque rating of 46.19 lb-ft, constraint 20’s requirements are also met as this results in a safety factor of 100%. <br><br>
### VFD Analysis
&nbsp;&nbsp;&nbsp;&nbsp;&nbsp;With the selection of the motor, the application of regenerative braking, with a VFD, becomes possible and suitable for testing desired parameters. This process is achieved by connected the variable frequency drive to the motor to apply a braking affect. This braking affect is produced by using the VFD to lower the frequency applied to the motor. However, simply lowering the frequency value does not result in the motor beginning to act as a brake. This is due to the synchronous speed rating of the motor. This rating is the speed at which, if exceeded, a motor will become a generator when driven by its shaft. This value is derived through the equation $N_s = \frac{(120)(frequency)}{Number Poles}$. The frequency and number of poles of the selected motor are, respectively, 60hz and 4 poles. With these values a synchronous speed of 1800rpm is found. The drum’s max rotational speed is 1288; therefore, this value must be stepped down to apply a braking effect to the system even at maximum speed. From the equation previously presented, it can be seen that the frequency directly affects the synchronous speed rating. Therefore, by using the VFD’s frequency control features, the required synchronous speed needed to switch motor operation to a generator can be controllably decreased or increased. This switch in operation is required in order to induce the desired braking effect. For, once the motor becomes a generator, the current will invert direction and backflow into the VFD. This will develop a counter torque and cause the motor to operate as a brake.<br><br>

&nbsp;&nbsp;&nbsp;&nbsp;&nbsp;In order to select and size the chosen VFD, different parameters were taken into account. The first, and main, factor that contributed to the selection of this unit included it being used also as a phase converter. Due to inputting single phase power into the VFD, it can not be simply sized based on its horsepower rating. Instead, it must be derated and selected based on its max output current rating. This stems from the conversion from 1 phase to 3 phase current being the (amperage*√3). Therefore, the need amperage rating is found by multiplying the motor’s full load amperage by the square root of 3. This calculation results in a current rating of 10.96 amps. This output current rating, for our implementation, must be less than or equal to the normal load current rating of the VFD. This is due to our system experiencing variable torque. Additionally, this rating must also be for a 1 phase (60Hz), 460 V input drive. Through the validation of these parameters, the Ironhorse ACG-4010 VFD was proven to be the best component for our system. For, its output current rating, with a 460 V, 1-Phase (60Hz) input, at normal load is 12.6 amps. With the selection of this VFD, the requirements for both constraints 22 and 23 are met.<br><br>

&nbsp;&nbsp;&nbsp;&nbsp;&nbsp;In addition, automation direct requires and suggests a line reactor to be used when using a VFD as a phase converter. However, we will be using a transformer to step up our 120 volt supply to 460 before feeding it to the VFD. This transformer will act as the line reactor required for this set up.<br><br>

### Braking Resistor Analysis
&nbsp;&nbsp;&nbsp;&nbsp;&nbsp;Due to this system operating on regenerative braking, current backflow will be present into the VFD. Therefore, operation must be put into place in order to dissipate the generated power. This will be done by connected a braking resistor to the DC Bus terminals of the VFD in order to dissipate this generated energy through heat. This is required when using a VFD, with a motor acting as a generator, due to the power back feed. This reverse flow into the VFD, if not properly dissipated, will cause the drive’s DC bus voltage to rise, resulting in over-voltage faults. This will lead to the drive protecting itself by shutting down, or possibly lead to damage to the input rectifiers. <br><br>

&nbsp;&nbsp;&nbsp;&nbsp;&nbsp;In order to select and size the chosen braking resistor, 2 main factors were taken into account. The first parameter is the minimum resistance value. This value won’t affect the resistor’s ability to dissipate the incoming power; however, it is vital to making sure it is compatible with the chosen VFD. This compatibility lies within the VFD’s internal brake chopper circuitry. This circuitry consists of a brake transistor that shunts excess current from the DC bus to the braking resistor. However, this transistor exhibits a maximum current rating listed within the datasheet. With this current rating and the over-voltage level of the VFD, the minimum rating of the resistor can be found through ohm’s law. The over-voltage level for the selected resistor is 820VDC. This value is 130%-150%  of the drive’s nominal dc bus voltage threshold. Therefore, the nominal dc bus voltage level is between 550 VDC and 630VDC. This puts the minimum resistance value of the resistor at 34.6Ω. The second parameter is the power dissipation capacity. This rating will ensure that the resistor is capable of handling the power sent to it from the VFD. For this rating, the maximum power of the bike is used (3500 W). With these required parameters, the Ironhorse GS-BR-1K5W043 braking resistor was selected. This resistor’s ratings for resistance and peak power are, respectively, 49 Ω and 12.4 kW. This component not only meets the required ratings, but also is the recommended component to use with the previously selected VFD. With these ratings, this component also meets the requirements of constraint 24.<br><br>

### E-Stop Analysis
&nbsp;&nbsp;&nbsp;&nbsp;&nbsp;Customer request and standard NFPA 79 – 10.7.1. require that an emergency stop be present in the event of dangerous situations. This requirement will be met through the process of implementing a emergency stop bush button wired to the stop terminal of the VFD's control circuitry. This wire setup is presented in the above schematics section. This system is powered by a 24 VDC source generated by the VFD's internal AC to DC converters. The P3 coil (stop coil) shuts off the VFD in the event that its power source is taken away. Therefore, once the button is pushed (opening the circuit) this coil will shut the VFD off. This will allow for an imediate stop to the VFD in order to protect it against whatever dangerous situation is occuring. This capability also allows the requirements of constraint 5 to be met.<br><br>

## BOM
|Item |Quantity |Price |Total |
|---|---|---|---|
|Dayton 3-Phase 5 HP Motor|1 |$888.03 |$888.03|
|Ironhorse ACG-4010 VFD|1 |$348.00 |$348.00|
|Ironhorse GS-BR-1K5W043 Braking Resistor|1 |$144.00 |$144.00|
|Automation Direct E-Stop Push Button|1 |$16.50| $16.50|
|Subsystem Total |||$1396.53|

## References
VFD & Braking Resistor Data Sheet: https://cdn.automationdirect.com/static/specs/acgdrives.pdf<br>
Dayton 3-Phase 5 HP Motor Datasheet: https://www.grainger.com/ec/pdf/36VF38_4.pdf<br>
Automation Direct E-Stop PB (Illuminated) (N.C contact) Datasheet: https://cdn.automationdirect.com/static/specs/cents22mmmush.pdf

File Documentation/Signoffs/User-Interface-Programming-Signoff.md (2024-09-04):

# User-Interface Signoff

## Functionality

The user interface will be the key system by which the user communicates with the test hardware/equipment. It will receive test parameter inputs from the user (ex: speed, throttle, braking), translate this data to the testing equipment, as well as communicate test results/metrics to the user. Further discussion will be addressed in the following sections.
## Constraints

The following are constraints imposed on this subsystem by different stakeholders in the project. They are explained in the section below:
|No. |Constraints |Origin |
|---|---|---|
|4| Be able to fully operate throttle control and dyno braking from an HMI/PC | Design Constraint |
|10|Display/capture values for bike speed vs time and torque vs time. |Design Constraint|
|15|Alert users of the potential risk of operating this chassis dyno system |Ethical Concern |

4: This constraint requests that the full testing operation of the stand be able to be completed without an individual physically on the bike operating it. This applies to this subsystem since the user interface controls the throttle and braking subsystems. 

10: This forces the design to find a way to take test data from the DAQ system, visualize it, and store it for later analysis. 

15: Constraint 15 addresses an ethical concern for safety, and the user interface is responsible for carrying it out due to it being the direct bridge between the dyno user and the test equipment. The solution is addressed in analysis.

## Schematics

### Hardware connections between PC, DAQ, throttle control, and braking:


### Sketch of the User Interface (LabVIEW front panel HMI):


## Analysis

In order to meet the constraints listed, the user interface will need to be able to take in user inputs for bike speed. It will then need to write this data to the respective subsystems through the DAQ card and begin the bike test run. Then, it will need to successfully read in data from the DAQ system and plot/store them along with the respective time via the PC. These needs can be met by utilizing National Instruments LabVIEW (graphical programming software) front and rear panels.

### User Input

For user input, LabVIEW software utilizes a front and rear panel. The front panel is the HMI layout where there will be the option to set a desired speed of 0-50 km/hr (from the customer). This front panel is what will be displayed on the PC during the test run, acting as the HMI. The user will be able to set up a custom duration test, or they will always have to option to change throttle/braking manually from here as well.

### Writing to Throttle/Braking Subsystem

Once the user chooses preferences for the test, the PC running LabVIEW writes to the DAQ. The LabVIEW VI code for the DAQ will be programmed to apply full-throttle (using PWM signals to the throttle system) until the bike’s speed reaches the designated speed. The DAQ houses 2 32-bit counters with the ability to perform pulse outputs (PWM). This speed will be maintained using closed-loop control, which is a commonly used tool in LabVIEW. Depending on the design of the braking/ torque measuring system, the VI will be programmed differently to control it. However, due to the versatility of LabVIEW, there is no issue in constraining another system to work within its uses. The schematic shows braking attached to an analog output, which is a likely possibility.

### Reading From DAQ

The HMI on the PC will also be designed to plot the different metrics that are relevant to the specific test being done. This data will be sent from the DAQ during the test, and displayed on the HMI (LabVIEW front panel). At the end of the test, (whenever the user ends the simulation on LabVIEW) the VI will write all of the time-stamped data acquired into an Excel/Matlab compatible file where it can be analyzed later. This is done simply by writing data into arrays and/or spreadsheets on the LabVIEW rear panel.  

### Safety Warning

To address constraint 15, the HMI screen will display a message regarding safety as the user begins the setup/input process. They will be prompted with: “Operating a vehicle on a dyno can be dangerous and cause great harm or death if operated incorrectly. Ensure the bike is securely fastened to the dyno and no loose objects are hanging near the bike. Push accept if you have ensured the bike is safe and secure for operation." After this has been accepted, normal testing operations may continue.

### Buying Software

Normally, NI LabVIEW would have to be purchased to be used. However, Tennessee Tech has a license for its use so this is not necessary for purchase.

### Wire Connections

The connection between the User Interface PC and DAQ is extremely important for this entire project. The BOM includes a 10ft USB-A to USB-B for connecting the DAQ to the PC (running LabVIEW).

## BOM

|Item |Quantity |Price |Total |
|---|---|---|---|
|10ft USB-A to USB-B Cord |1 |$ 9.99 |$ 9.99|
|Subsystem Total |||$ 9.99|

*User-Interface Subsystem will utilize the DAQ purchased in DAQ subsystem

## References

USB Cord:
https://www.amazon.com/Printer-Braided-Keyboard-Controller-Microphone/dp/B095HPPZ4G?th=1 

NI USB-6215 DAQ Specs:
https://www.ni.com/docs/en-US/bundle/usb-6215-specs/page/specs.html

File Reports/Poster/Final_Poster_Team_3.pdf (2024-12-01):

# Electric Motor Dynamometer

Dylan Scruggs, Andrew Copeland, Aaron Littleton, Ethan Griffith, Branson Stephens, Jonathan Haas
Tennessee Technological University

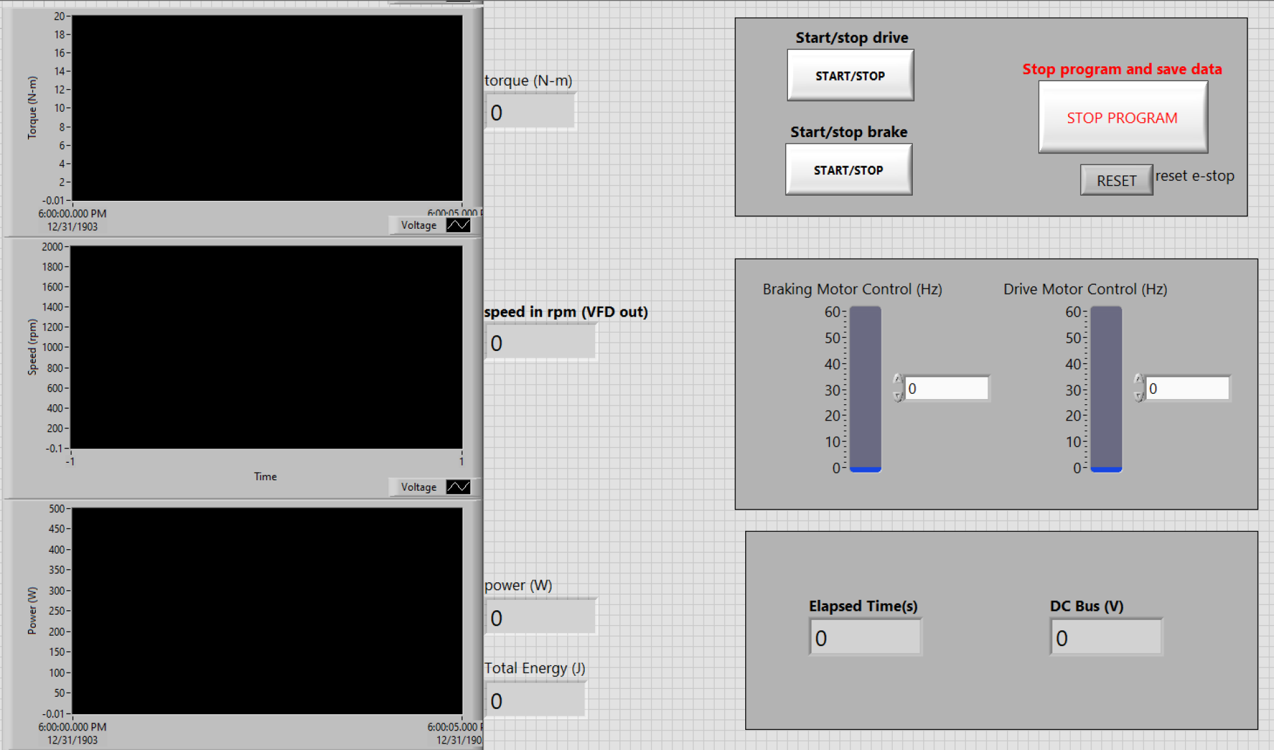
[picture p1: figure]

## Introduction

Problem Statement
The objective of this capstone project was to develop a user-controlled system capable of deriving the key desired motor metrics: rpm, torque, and power under varying conditions. Originally, this was assigned to be a chassis dynamometer to test electric motorcycle metrics, but due to customer and time constraints, the system was downsized.
Overview of Constraints
The system must provide a controlled, constant resistance to the device under test while collecting and displaying precise, accurate data on a user-friendly interface. The implementation shall also follow all applicable NEC codes and regulations.

## Design

## The Team

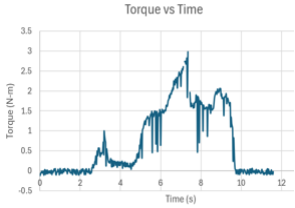
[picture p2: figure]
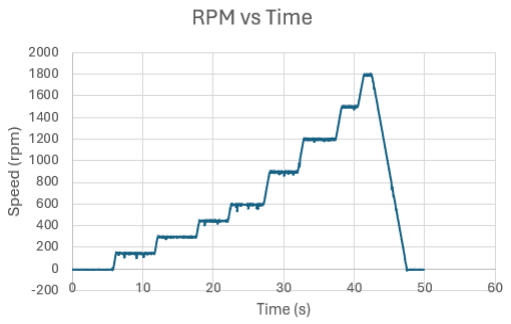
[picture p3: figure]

## Conclusion

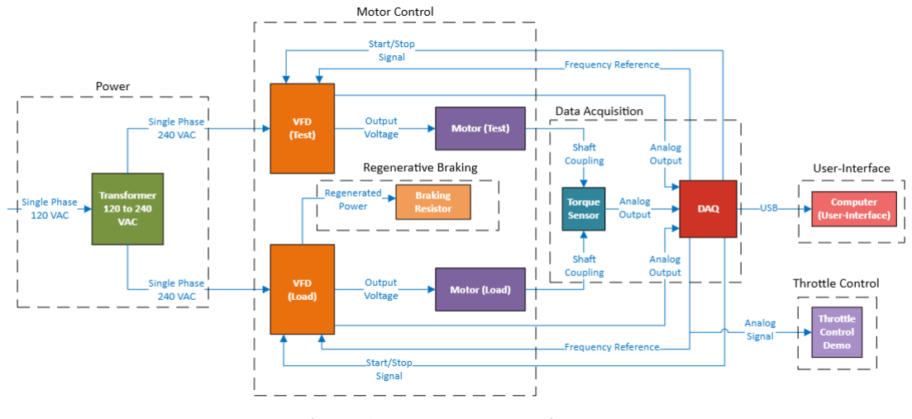
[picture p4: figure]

- Power: A 1kVA transformer was used to step up the single phase 120 VAC, from the wall, to 240 VAC. The VFDs were then derated and utilized to be phase converters.
- Motor Control: A Τ
1

3 HP and a Τ
1

2 HP induction motor are each controlled by separate Yaskawa 1000 series VFDs.
- Regenerative Braking: Any regenerated power, during braking, is dissipated through a 400-watt braking resistor.
- Data Acquisition: A rotary torque sensor and the VFDs were used to extract raw data signals, and the NI USB-6215 then took in and converted these into readable values.
- User-Interface: LabVIEW was utilized to appropriately display all data and control the system.
- Throttle Control: A Nema 17 stepper motor, driven by a A4988 drive and Arduino, controls a 3d printed clamp to display throttle position reference to motor speed.

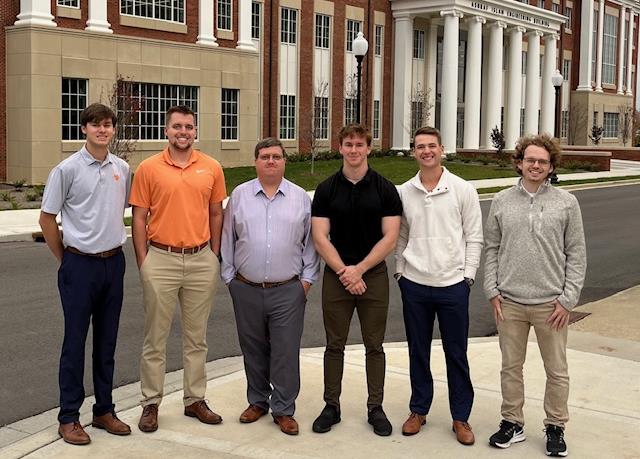
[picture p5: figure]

From Left to Right: Andrew, Aaron, Jonathan, Ethan, Dylan, Branson

Fig. 1 System Block Diagram

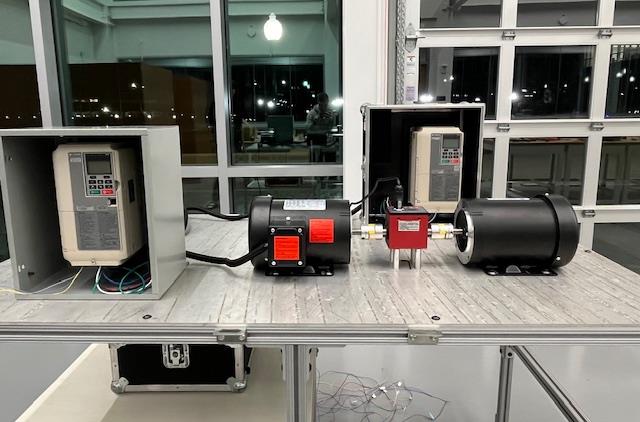
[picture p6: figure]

Fig. 2 System Layout

## Experimentation

Capabilities:
- The DAQ is able to read and display rpm, torque, and power accurately and precisely, to the thousandths, with little to no noise.
- The system is able to be moved and run on 120 VAC due to the transformer and the VFD’s phase conversion capabilities.
- Any user can fully operate the system from his/her laptop with the constructed LabVIEW code.
- All data, upon testing completion, can be saved and later analyzed in an Excel file.

The team has successfully constructed and proven the capabilities of the electric motor dynamometer. As a result, this design is now capable of being expanded and integrated to fit the desires of the electrical motorcycle chassis dynamometer by future teams.

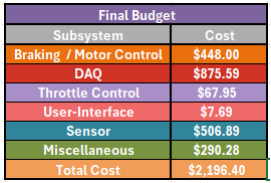
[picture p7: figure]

We would like to specially thank Professor Micah Rentschler for his constant support and advice throughout our design. We also would like to thank the College of Engineering for their guidance and support.

Fig. 4 RPM Graph (Excel) | Fig. 5 Torque Graph (Excel)

The system utilizes LabVIEW and Excel to display and save all recorded data from each test.

Fig. 3 User-Interface Screen

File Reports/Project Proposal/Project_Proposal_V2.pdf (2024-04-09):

# Electric Motorcycle Test Station

Andrew Copeland, Ethan Griffith, Jonathan Haas, Aaron Littleton, Dylan Scruggs, Branson Stephens Electrical and Computer Engineering Department Tennessee Technological University Cookeville, TN
awcopeland42@tntech.edu, ecgriffith42@tntech.edu, jdhaas42@tntech.edu, ajlittleto42@tntech.edu, dascruggs42@tntech.edu, bkstephens42@tntech.edu
I. INTRODUCTION
The use of motorcycles in developing countries has become one of the main sources of transportation as 88% of the worldwide two and three-wheelers are found in low- and middle-income nations [1]. However, the price of owning a gas-driven motorcycle can become overwhelming and cause financial issues for users within these nations. In response, manufacturers have shifted their focus to producing electric vehicles (EVs). Although shifting to lower maintenance and fuel costs, recent statistics show that EV bike prices directly reflect the most sought-after characteristic: range. Displayed in figure 1 is the ratio of dollars per kilometer for the top 10 electric motorcycles with the best range, ranked by TopSpeed, in 2023 [2]. As seen from this, consumers must fork over, at minimum, $50 per kilometer of range in these bikes. To address this expense, Proton Power is aiding in the design of an EV motorcycle that will travel 400km on a single charge at a considerably lower price of $10,000 ($25 per kilometer). To aid this production, this project proposes creating a dynamic data acquisition (DAQ) test station. The application of dynamic data acquisition is frequently used amongst various testing technologies as it allows for ensured accuracy and reduced errors. One prominent example of DAQ is its implementation into dynos. Similar to dynos, this project will evaluate the capabilities of the full motorcycle and output the captured data to a real-time display. Through the coaction of a DAQ and other subsystems, this project presents a design that will allow testing to be conducted on the bike in order to prove the capabilities of Proton Power’s newly produced batteries.

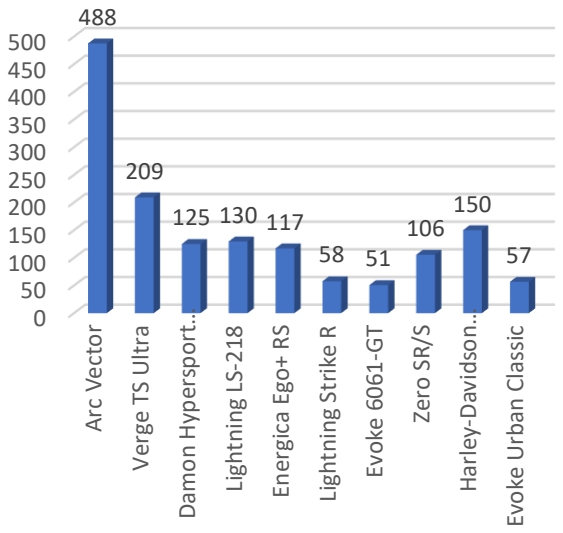
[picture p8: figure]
Arc Vector; Verge TS Ultra; Damon Hypersport…; Lightning LS-218; Energica Ego+ RS; Lightning Strike R; Evoke 6061-GT; Zero SR/S; Harley-Davidson…; Evoke Urban Classic

Fig. 1. Dollar per kilometer for notable electric motorcycles [2]

II. THE PROBLEM
Over recent years, the push to shift towards the use of EV vehicles has risen (Fig. 2.) [3]. With this, extensive tests, to ensure product quality, must be conducted. In most circumstances, a chassis dyno is used to extract the desired characteristics. These features being measured consist of properties such as torque output, horsepower, air/ fuel ratios, oil temperature/pressure, and water temperature [4]. However, when applying the same system to an EV vehicle, all these combustion engine specifications are not needed. From this problem stems the proposal of creating an EV-rated test station. This project will allow for efficient, accurate testing to be completed on EV-specific components to grant the ability for bike enhancements. To further expand the bike’s ability to be improved, a mathematical model will be created to allow for the derivation of equations. These will be used to simulate different inputs and their outputs. To attain an accurate model of the motorcycle, various problems must be addressed such as measuring torque/acceleration/power/ etc., sensor selection, powering the EV bike, data acquisition/analysis, and simulating different road grades. Each of these issues will be addressed in compliance with the standards and constraints set by the stakeholders.

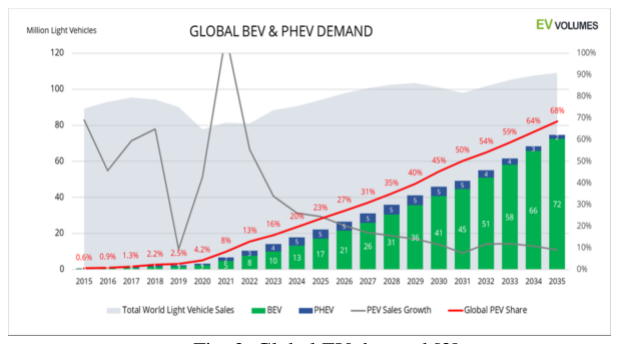
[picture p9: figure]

Fig. 2. Global EV demand [3]

A. Background
1. Measuring torque, acceleration, power, etc: To provide an accurate mathematical model of the function of an electric motorcycle, one would need to obtain an array of abundant information from the bike. Torque, acceleration, and angular velocity are just a few examples of common parameters tested using a chassis dynamometer [5]. Dynamometers (dyno for short) typically measure torque by using a device called a torque arm, which measures the force needed to move the dyno (with a load cell) [6]. This value can be output by the load cell to any microcontroller. The acceleration of a bike can be measured simply with an accelerometer attached to its wheel, and it could also be measured using a wheel speed sensor by taking the derivative with respect to

## Dollar per Km Ratio

time. To measure power, there is a formula that can be used with torque and rpm as parameters:

HP =

(Torqueft−lbs)(SpeedRPM)
5252

RPM (revolutions per minute) of a motor is another measurable parameter that can be found with a tachometer, either electrical or mechanical.

2. Sensor | selection: | To | gather | specific | bike
measurements, an assortment of sensors must be used. However, selecting the sensor most suitable for the element being measured is a challenging task. The first step in choosing the correct sensor is
understanding | the | two | main | applications.
Microcontrollers accept, based on their input, two main types of sensors: digital and analog [7]. Each presents its own advantages and disadvantages. Of these applications, digital sensors are favored for their precision, accuracy, and adaptability [8]. Digital sensors allow for information to be digitally converted from analog physical data to discrete values and then communicated. This is done using digital components such as logic gates and chips. The result is then, in most cases, provided in terms of binary output. Unlike digital, analog sensors provide indiscrete, continuous signals. These signals are precise and directly proportional to the unit being measured [8]. To extract, analog uses components found in traditional circuits such as resistors, capacitors, inductors, and more. Scenarios in which real-time data is required are where analog interfacing is most found as the output is constantly changing.
3. Powering the EV bike: Being able to run tests over an extended period is a crucial factor in understanding the bike's performance. To allow this, a power supply can be implemented into the system to continuously supply power to the bike. With the specifications of the bike, a DC voltage is required to correctly input a power source. This requirement can be met by using an AC-to-DC power supply (given the test station is receiving AC input). Two main types of AC to DC power supplies are used: linear and switching. For a linear supply (shown in Fig. 3), AC-supplied input is converted to DC by using a transformer to reduce the AC input to a usable value for the intended application. The reduced voltage is then rectified and converted to a filtered DC value [9]. For a switching supply (shown in Fig. 4), the process of reducing the input voltage is eliminated and is instead rectified and filtered at the input. Then, the converted DC value goes through a chopper to convert voltage into a high-frequency train [9]. This wave then is converted back to DC voltage through another rectifier and filter. Within this design, an isolation transformer is used to prevent dangerously high voltage from passing to the output. Between these two different processes exist different advantages and disadvantages. Linear power supplies require large, heavy transformers, whereas, switching supplies use much smaller, lighter transformers. Switching supplies also prove more efficient as linear supplies lose more energy as heat [10]. However, linear supplies have more elementary circuits, causing them to cost less, than switching supplies.

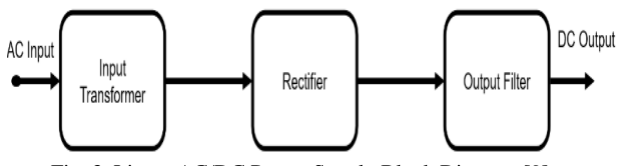
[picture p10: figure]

Fig. 3. Linear AC/DC Power Supply Block Diagram [9]

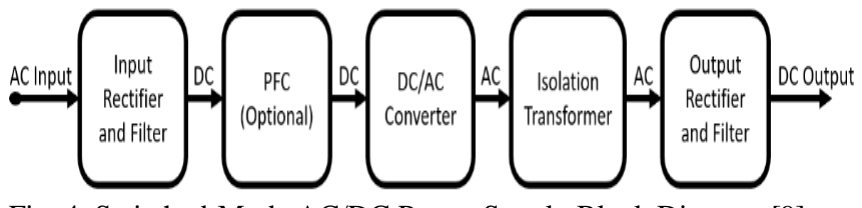
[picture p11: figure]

Fig. 4. Switched-Mode AC/DC Power Supply Block Diagram [9]
4. Data acquisition/analysis: Once a sensor has gathered information and outputted it to a microcontroller, the input must be processed. Different sensors measure different information; therefore, the data must be processed in the correct way to allow output in the most usable form. This process typically begins with an analog signal being converted into a digital signal using an ADC (analog to digital converter). Analog signals must be converted to digital signals for the microcontroller to be able to store and “understand” the data being sent in [11]. Depending on the type of output the sensor uses, the controller will have to be programmed to convert the value it receives (voltage for example) into a corresponding unit. From this point, the data can be output onto visual tools such as graphs or charts where it will be easier for a user to decipher what the sensor is conveying.
5. Simulating different road grades: When testing any type of vehicle, it is important to test the effect of different inclines and declines. The most common way to simulate this is by using a chassis dynamometer. Without adding any extra mechanical parts to a dyno, the road grade can be simulated by taking the 0% grade data and having software alter it based on the desired slope. Another way dyno companies address this is by adjusting the load resistance, with a motor, applied to the wheel (one company refers to this as “load mode” [12]). This resistance, when increased, raises the engine demand to simulate uphill. To simulate a degrade, the motor supplies rotation to the rotating cylinder. However, this requires calibration, so the operator knows what resistance refers to what road grade. Aside from the typical chassis dynamometer, car companies have simulated steep grades using a sled dynamometer [13]. This is a device (like a trailer) pulled by the vehicle that with the ability to change its own weight. This is done by adjusting electromagnetic coils in the trailer that make it easier or harder to pull, much like driving up a hill. This allows testing automobiles on different grades while on flat ground.

B. Stakeholders
This project will have two types of stakeholders. There are direct stakeholders who will be able to edit the GitHub repository, have meetings with the team, and have direct input on the project. There are also indirect stakeholders who are identified as being impacted by the project but will not have direct input on the project itself.

Direct Stakeholders
- Proton Power
- Supervisor, Professor Roberts
- Project Team

Indirect Stakeholders
- Consumers of the product
- General public by reduced emissions and noise pollution.
C. Specifications
The customer for the project, Proton Power, has verbally expressed some requirements that they have for the motorcycle testing station. The motorcycle they want to test is a Bob Eco two-wheel electric motorcycle.
1) Power the motorcycle: While the motorcycle is being tested on the stand, it should be powered using an external power source. The typical standalone power for the motorcycle discussed is a battery providing 65 volts/10 amps (see appendix figure 8).
2) Mobile Stand: Proton Power requests that the testing stand be a non-permanent structure. This will allow them to move it if they ever need to. This also allows the team to build the testing stand on Tennessee Tech’s campus.
3) Obtain testing metrics: The testing stand needs to effectively obtain values for, specifically, the test article’s torque, acceleration, and velocity. Other additional data will be tested to allow for an accurate modeling of the tested motorcycle’s dynamics. This stand will also need to measure the inputs that relate to the output’s testing metrics. An extra request made by Proton is to have the stand simulate different
road | conditions | for | the | bike, | referring | to | road
grade/roughness.
4) Display testing metrics: The testing stand will also need to take the values tested (inputs/outputs) and display them visually as the bike is running. They request this be done using software-aided graphs or charts.
5) Obtain a mathematical model: The goal of the testing stand requested by Proton Power is to make an effective model of the functions of this electric motorcycle; therefore, they have requested that a mathematical model for the Bob motorcycle be generated.
6) Operate safely: The customer has clearly stated they need the testing stand to operate safely and abide by all relevant codes and conducts.
D. Constraints
The constraints that define the scope of the project and deliver on the expectations expressed by the customer are that the test stand design shall:
1. have a footprint that the testing apparatus can occupy in the Proton Power factory.
2. be able to be transferable and not permanently fixed to one location.
3. be able to safely operate the motorcycle up to speeds of 60 km/hr.
4. be able to monitor temperature effects on the bike and subsystems to prevent damage from excessive temperatures due to the testing environment.
5. capture current and voltage supplied to the drive motor along with vehicle speed, torque, horsepower, and rpm and display all results.
6. be able to fully operate remotely.
7. be able to supply the motorcycle with 65VDC with a 10A capacity.
8. be able to simulate various vertical inclines/declines up to ±19 degrees.
9. comply with all relevant codes and standards listed in Section E below.
E. Standards
Within the IEEE, NFPA 79, NEC, IEC, and OSHA codes, a comprehensive list of possible standards and regulations is provided that must be complied with. Below these are listed but not limited to:

NEC 310-16, National Electric Code Wire Current Ampacity Table – This standard will be used for determining conductor sizes. It provides comprehensive guidelines for the sizing of conductors based on the amount of current they can hold, the voltage rating, and the insulation type that is used. Adhering to this standard will ensure that the conductors used are appropriately sized to handle the electrical loads while maintaining safety and reliability.[14]

NEC 430, Motors, Motor Circuits, and Controllers -This standard covers all the requirements for the installation and protection of motors and associated circuits. It provides rules for the sizing and protection of overcurrent devices (breakers) and motor controllers to ensure that all motors operate safely and according to standards. This will be a crucial aspect of the project especially when testing the attributes of the electric motorcycle's motor and motor controllers. Adhering to this standard ensures that all equipment involved with the motor and the motor itself will be operating safely [15].

NFPA 79 – 10.7.1, Emergency Stop & Stop Devices – This standard ensures that in any electrical working environment of industrial machinery, there must be a stop or emergency stop pushbutton easily accessible. This will allow for safe operations of systems in the case of emergencies [16].

NFPA 79 – 9, Control Circuits and Control Functions
– This standard covers control circuit supply, voltages, start functions, and stop functions. Section 9.2.5.4 covers emergency stop requirements [16].

IEC 62196-1 - This standard dictates how plugs, socket-outlets, vehicle connectors, and vehicle inlets are managed specifically for charging electric vehicles. With this standard, it will be ensured that the charging methods align with international safety standards. By following these guidelines, it will be guaranteed that the compatibility between charging equipment and electric motorcycles, facilitates an ideal and efficient charging process [17]

IEC 60204 - This standard is an international standard that specifies safety requirements for electrical equipment and control systems used in machinery. It covers aspects such as electrical installations, wiring, protection against electric shock, and control circuitry. Complying with this standard will ensure that the electrical systems and equipment in machinery meet safety standards and minimize the risk of electrical hazards [18].

IEEE 2700-2017 – Covers a framework for sensor performance specification terminology, units, conditions, and limits [19].

OSHA | 1910.303 | - | This | standard | provides
comprehensive guidelines for electrical installations in general industry. It focuses on the health and safety of all personnel and systems used. By adhering to this standard, the protection of all personnel involved against electrical hazards such as shocks, fires, and explosions will be avoided. Safety is of utmost importance so complying with these standards will be a priority [20].

OSHA 1910.147 - This standard ensures the safety of all personnel involved in any electrical work. It provides comprehensive guidelines for the control of hazardous energy sources to prevent accidental startup of machinery or equipment, which could lead to serious injuries or fatalities. By using this standard, it will establish procedures for the isolation and control of electrical energy sources during maintenance, repair, or testing activities [20].

IEC 61439 - This standard is an international standard that specifies requirements for the design, testing, and performance of low-voltage switchgear and control gear assemblies. This standard provides a safety guideline for electrical equipment used in power distribution and control applications This standard provides useful methods for the design and construction of switchgear and control gear assemblies within the test stand, ensuring the safety for operation of electrical components such as control panels, distribution boards, and power distribution systems [21].

F. Challenges
Some challenges will be the brief time constraint and an unknown budget. This time constraint will be amplified due to the team’s current limited knowledge of the project. Another challenge that is foreseen is simulating the motorcycle traveling on a non-flat road. There is also the issue of the location of Proton Power. The design of the test stand will have to consider the space available at Proton’s plant without being able to physically verify any details. Along with this, there is the major challenge of communicating with the customer, supervisor, and all of the project team members. Every one of the parties has a busy schedule, and it will constantly be a challenge to keep all on the same page in terms of the details of the project.

III. SOLUTION

A. Unknowns
One significant unknown for the project is the power supply for the motorcycle. The lithium-ion battery that comes installed in the motorcycle will be swapped for a solid-state battery designed by Proton Power. The specifications of each battery and how they may differ are unknown. The variance of characteristics could have numerous implications on things such as runtime, charge time, overall weight, and thermal properties. The specifications for each battery will be vital to producing an accurate software model of the motorcycle. An additional component to this unknown is the condition of the motorcycle when the team receives it and whether there will be both a battery and charger included to begin testing with or not.
Another factor unknown is the tire performance specifications. The rear tire will need predictable traction to
deliver | accurate | metrics | while | operating | on | the
dynamometer.
The vehicle's vibration during operation throughout a range of rotations per minute at an unknown intensity can cause numerous issues with electronic sensing devices and potentially also a loss of traction. The effects of vibration on the sensors of the dynamometer could range from degradation of accuracy to complete device failure. To deliver accurate measurements, these insecurities must be monitored and addressed throughout the design and testing process. Thermal effects are also an unknown factor. The motorcycle is designed to operate in an open ambient environment with some airflow value as the vehicle is operated. While testing in a closed environment, lacking any significant amount of airflow, the increase in temperature of multiple components could create unforeseen effects. Therefore, an evaluation of components that could be prone to a negative influence of thermal effects will need to be performed, and adequate countermeasures will need to be taken.
The vehicle must also deliver metrics simulating operation on an incline or decline. The rate of incline or decline will need to be specified by the customer and the team will need to develop a design sufficient to support these requirements.
B. Existing Solutions
An important aspect of designing and developing the DAQ stand is to survey existing solutions within research literature, the current market, and the industry. By examining and
analyzing | solutions | found | in | similar | projects, | a
comprehensive | understanding | of | the | background
information, standards, and challenges that may affect the project can be collected and better understood.

The most common method for testing different data outputs on a bike is the use of dynos. These are bike test stands that measure the engine output of the bike. These are commonly sold on the market and used for data collection for data sheets, testing to determine potential upgrades and improvements, and even for racing bikes. While some aspects of this DAQ stand will be similar to other dynos on the market, it will differ by giving specific and personalized data requested by Proton Power and having the unique feature of being designed specifically for electric bikes in the Bob Eco supply line.

Commercial Solutions
- EASYRUN Test Benches – These are high-quality bike stands and the mechanical design of the stand is exceptional, but they are made for racing bikes and not electric bikes. While these may be efficient for racing companies, they are not designed to test EV bikes [22].
- BAPRO Motorcycle Dynos – These are test stands that provide a wide variety of tests and simulations for bikes including electric bikes. It has options for both a two-roller testing system and a single-wheel roller testing system. Its main feature is specializing in providing certificates for testing that can be used when reselling. The downside to this system is since it is such a wide variety of testing not only is it extremely expensive, but it is also large, hard to move and transport, and very heavy [23].
- LAMNEC Electromechanical Technologies – This solution provides the unique advantage of being able to order any testing equipment needed separately along with being able to order the test stand as a whole. However, this company is based out of China and shipping test stands can be difficult. These stands also do not measure the electrical side of the bikes only the mechanical side. The cheapest ones purchasable are over $20,000 [24].
- DAIG4 – This smart power bench must be operated by trained personnel. It gives several engine specifications but is for mechanical engines and not designed for EVs. It provides exhaustive tests on the engine loads under specific road conditions. This bike stand is used for tuning and modifications for engines. Like with most test stands while this is a great stand for gas engines this does not transfer over to EV bikes, and it is not commercially available for sale to the public [25].

From these examples, it is clear to see that there are a few products on the market similar to the design that is going to be achieved in this project. However, while these existing products are well-designed to accomplish the desired specifications that they were intended to, they do not match the specifications and design that Proton Power wants for their DAQ bike stand. There are no commercially available products on the market that fit the exact specifications that are wanting to be achieved by Proton Power. This is the motivation to have a specific design for the DAQ stand that will be specifically tailored to Proton Power’s needs.

C. Proposed Solutions
The following section will outline multiple proposed solutions to fulfillthe deliverables provided by Proton Power. Given the information provided, each solution is subject to change pending a set list of design specifics. However, each presented plan is selected based on feasibility and the
specifications | and | constraints | presented | previously.
Additionally, all following proposals aim to minimize the previously stated risks and impacts, within listed unknowns, and deliver set measures of success.
1) Quantifying required metrics: Acquiring the required metrics with peak accuracy and precision is pivotal to reaching the optimal end product. Numerous sensors, all exhibiting different qualities, exist to generate these outputs. The first option consists of implementing various sensors to derive each measurement. This allows for all desired data to be found with the implementation or use of separate sensors. Torque, the most important measurable, has various methods of being obtained. However, the cheapest and most suitable application for this system is to use an anti-rotational torque arm with a load cell transducer integrated into the system. Additionally, acceleration can be calculated through the use of a speed sensor and calculations. Power, with these obtained results, can also be calculated. This solution produces the customer’s expressed desired values at a reduced cost in comparison to other systems. One drawback to this procedure is the increased design and integration time. A second option consists of purchasing and using a rotary torque sensor to measure torque and rpm. This would simplify the process of implementing multiple sensors and still allow for further values to be computed. However, due to using a torque sensor to measure the reading from the chassis, the rpm output will actually signify the rotational speed of the tire (angular velocity). To be able to obtain acceleration and power values from this data, mathematical computation must be used to convert the angular velocity to linear velocity. This implementation, although raising the cost of the project, saves a large magnitude of time. Another alternative solution suggests that the sensors already within the bike be decoded and used to run tests. This solution would allow for a large sum of money to be conserved. However, with the deadline presented this solution currently proves to be infeasible. Building on the feasibility of each solution, both previously mentioned options are suitable given the time constraints. However, depending on the budget, the preferred method would be to use a rotary torque sensor to obtain all desired metrics.
2) Supplying power: To allow extended tests to be run on the bike’s longevity, constant, consistent power must be supplied. The rated values at which the bike requires is 65 VDC with a 10 ampere capacity. In order to provide these specifications, a power supply must be used. The easiest and least time consuming proposition would be to purchase and implement a 65 volt, 10 ampere switching power supply. One vast advantage that follows the simplicity of purchasing and connecting a supply consists of reliability. Manufactured power supplies undergo meticulous tests to ensure the ability of the device. Alternatively, the ability to design and construct a power supply specific to the parameters listed is also available. This would allow for a precision factor, incomparable to off-the-shelf models, to be present. Although this would provide a device tailored to this specific project,
with | the | time | constraints | and | currently | provided
specifications this method, as of now, lacks feasibility. The cost of constructing a power supply also proves to be upscaled compared to purchasing a reliable unit. With this, purchasing a reliable power supply is justified to be the preferred, current plan of action.
3) Data acquisition/analysis: Once all the sensors/ measurement devices are in place on the stand, they will have to be read from and get the information analyzed. This can be done using microcontroller/microprocessor boards. A proposed solution to this would be to utilize two boards. All the testing information from the various sensors could be sent via wire to an Arduino-based microcontroller to begin. These boards are equipped with analog-to-digital converters which would be needed if interacting with analog sensors. However, Arduino-based boards are inferior to Raspberry Pi microprocessors when it comes to data logging and graphing [26]. Along with this, a Raspberry Pi processor is not equipped with analog-to-digital converters like an Arduino. This leads the team to propose using one of each type of board to effectively capture the data produced by the testing station. The data would be sent into an Arduino board, converted to digital if necessary, and then transferred over to a Raspberry Pi to be processed, analyzed, and displayed on a monitor of some sort. This would also allow for the data to be put into different software such as MATLAB or Python where a mathematical model for the bike could start to be created using all the various inputs/outputs. Another solution to this would be instead of using two different controller/processor boards, it is possible to only use one Arduino board for this proposed solution. It would also be possible to use a singular Raspberry Pi processor with externally connected analog-todigital converters to interface with sensors and process data. After seeing the availability of ways to solve this problem, it can be said that this portion of the project is fairly feasible.
4) Simulating road grades: The test stand will have to simulate moving vertically to be able to acquire data at various road grades. One method will be adding resistance to the roller so there is more demand on the motor to simulate the vehicle going uphill. To simulate going downhill the team will use an electric motor that will move the roller and vehicle so there is less demand on the motor. The other option is to create a model for various road grades through real-world testing. The team will use the mathematical model to have various outputs at a given speed at a given road grade. This will involve recording data such as speed and output power of the motor at different road grades then creating a model from the test data to be able to simulate going up or downhill. The first option will cost more but will be more precise and save time compared to finding and measuring the locations of various road grades, riding it at the various road grades, and then creating a model that would not be exact due to the numerous variables active while testing. Another benefit of the first option is that something similar has already been done successfully [27]. The main benefit of creating the model would be cost savings.
D. Measures of Success
The following measures of success address each previously mentioned constraint in corresponding numerical order and describe how the team planned to meet each constraint and verify it was met by the following testing method:
1. The apparatus successfully fits within the intended location at the Proton Power Facility.
2. The apparatus is able to be relocated and is not permanently fixed at any location of operation. This test can be performed by moving the entire apparatus and performing all operations.
3. The motorcycle will be able to be installed, operated, and removed safely with no immediate danger to personnel. This test can be proven by the apparatus not having any pinch points or sharp edges, and the motorcycle can be safely and securely operated up to 60 km/hr.
4. The vehicle can be operated at a time and condition specified by the customer’s intended use without incurring any damage to any subsystem of the vehicle or testing apparatus.
5. Be able capture current and voltage supplied to the drive motor along with vehicle speed, torque, horsepower, and rpm. Values captured should match the corresponding values displayed from the motorcycle’s internal DAQ and the anticipated values provided from the motorcycle specifications.
6. No personnel will need to be present in or on the testing apparatus to operate all the desired functions of the vehicle during testing. Vehicle testing can be performed initially and repeatedly without any physical interaction other than the initial setup.
7. The original battery installed in the motorcycle provides 65VDC at 10A capacity. The design will need to support power at that capacity, using the factory battery or designing a power source that will be sufficient to meet these requirements. The power supporting the motorcycle can be verified at the input with a voltmeter and ammeter.
8. Be able to control torque resistance to simulate a ±19-degree incline or decline.
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

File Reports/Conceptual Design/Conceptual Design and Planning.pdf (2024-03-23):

# Electric Motorcycle Testing Conceptual Design

Andrew Copeland, Ethan Griffith, Jonathan Haas, Aaron Littleton, Dylan Scruggs, Branson Stephens Electrical and Computer Engineering Department Tennessee Technological University Cookeville, TN
awcopeland42@tntech.edu, ecgriffith42@tntech.edu, jdhaas42@tntech.edu, ajlittleto42@tntech.edu, dascruggs42@tntech.edu, bkstephens42@tntech.edu
I. INTRODUCTION
Electric Vehicles (EVs) are evolving and exhibiting a presence in all areas of the world. With this development, there is difficulty in complying with the various charging requirements to support worldwide usage. To address these challenges, Proton Power is developing a battery that will demonstrate significantly faster charging and expanded range. In response, this project will display the utilization of an integrated data acquisition system (DAQ) into a constructed chassis dynamometer to obtain important data to enhance and prove this battery’s capabilities. Correctly choosing and integrating sensors into the system is a predominant factor in receiving accurate input and delivering the optimal output. Therefore, extensive testing will take place throughout the design. In addition to ensuring product effectiveness, the device must comply with necessary standards and engineering ethics to validate overall safety. In the following sections, this conceptual design will precisely outline the overall system but allow fluctuation in decisions considering certain hardware and software selections.
A. Formulated Problem Statement
This dynamometer system is expected to capture the data necessary to develop a software model of the motorcycle. This model will mathematically predict the differences and impacts of changing the battery types that supply power to the motorcycle. The function constraints and expectations of the dynamometer are listed below. The dynamometer shall:
1) Be transferable and not permanently fixed to one location.
a. This constraint comes from Proton's request to ship the apparatus to various locations.
2) Be able to safely operate the motorcycle up to 85 km/h.
a. This constraint comes from the specification sheet of the Bob motorcycle, which states a max speed of 85 km/h (see appendix Figure 6).
b. The stand should be able to support safe operation up to speeds of at least 85 km/h.
3) Capture and display relevant testing data in real-time and be transferable.
a. This is a requirement from Proton to monitor and operate the motorcycle effectively and efficiently.
b. Having transferable data allows Proton to share the motorcycle's capabilities with other parties.
4) Be able to be fully operated remotely.
a. This constraint was created for safety and approved by the customer.
b. This allows the stand to test a motorcycle with minimum safety risk to operators.
5) Comply with all relevant codes and standards listed in II. Ethical, Professional, and Standard Considerations, Section B below.
a. This is required to ensure safe operation and compliance with all relevant regulations.
6) Contain a standalone harness with sensors that can be temporarily fixed to the bike to verify the dyno data.
a. This requirement comes from Proton to verify the accuracy of the measurement from the dyno stand.
b. This constraint also incorporates redundancy, which will identify sensors on the dyno or harness that distribute inconsistent data.
7) Support incline/decline testing up to 8% road grade.
a. This constraint comes from Proton wanting to verify the motorcycle’s ability to handle different road grades (hills).
b. This requirement contributes towards developing a model of the motorcycle’s dynamics.
8) Support repeatedly testing the bike from 0km/h to 50km/h and then back down to 0km/h.
a. This constraint is a direct request from Proton.
b. These are specified values required to build a Hamiltonian model of the motorcycle.
9) Be able to adjust operating speed in 1km/h increments and measure response time.
a. This constraint is a direct request from Proton.
10) Display values on a single PC using pre-existing dyno software.
a. The PC display is a customer requirement to see the data being gathered.
b. The customer advised using existing dyno software to prevent too much time spent developing software.
c. This could prevent the project from being completed within the capstone duration.
d. The customer agreed the team should find something available to purchase.
11) Support weights up to 400kg on the motorcycle.
a. This constraint is a testing requirement given by Proton.

b. The customer wants to test the motorcycle with various weights up to 400kg.
12) Be tested with motorcycle batteries having a charge of at least 50% capacity.
a. This is a constraint from Proton.
b. The motorcycle should not be tested with batteries with less than a 50% charge.
13) Be able to simulate the braking system of the motorcycle.
a. The customer has specifically requested the ability to conduct brake testing from 50 km/h to 30 km/h.
14) Support the motorcycle being powered and operated with the original 72V-20A batteries until the prototype batteries are available.
a. The customer plans to have new battery technology available for testing in the Fall of 2024.
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

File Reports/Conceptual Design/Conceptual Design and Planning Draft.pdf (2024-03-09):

# Electric Motorcycle Testing Conceptual Design

Andrew Copeland, Ethan Griffith, Jonathan Haas, Aaron Littleton, Dylan Scruggs, Branson Stephens Electrical and Computer Engineering Department Tennessee Technological University Cookeville, TN
awcopeland42@tntech.edu, ecgriffith42@tntech.edu, jdhaas42@tntech.edu, ajlittleto42@tntech.edu, dascruggs42@tntech.edu, bkstephens42@tntech.edu

INTRODUCTION
Electric Vehicles (EVs) are evolving and exhibiting presence in almost all areas of the world. With this development, there is difficulty in complying with the various charging requirements to support worldwide usage. To address these challenges, Proton Power is developing a battery that will demonstrate significantly faster charging and expanded range. In response, this project will display the utilization of an integrated data acquisition
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

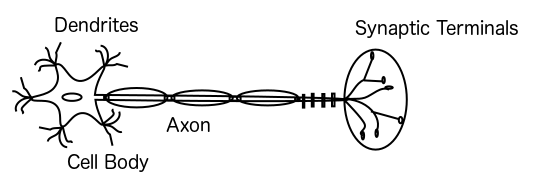
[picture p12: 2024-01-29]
Reports/Poster Template/Images/Neuron.png

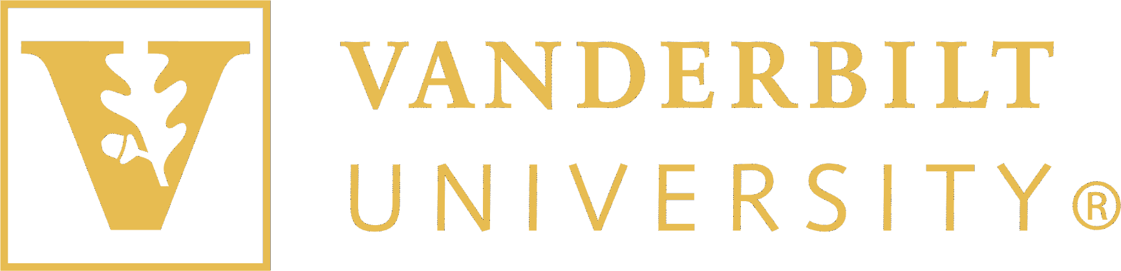
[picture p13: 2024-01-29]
Reports/Poster Template/vandygoldoverunder.png

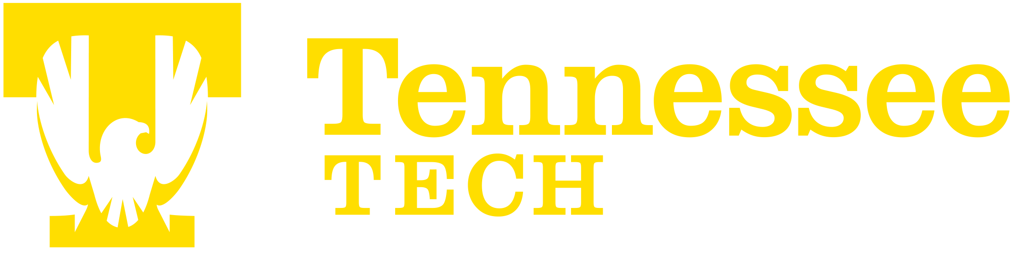
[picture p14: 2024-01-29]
Reports/Poster Template/tntechgold.png

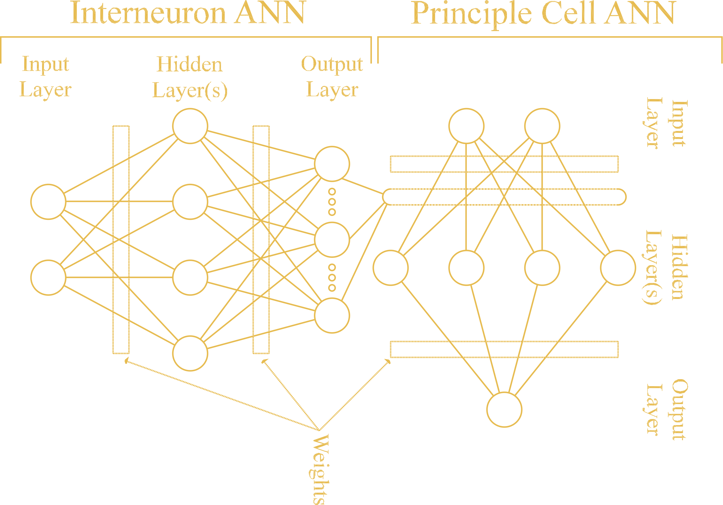
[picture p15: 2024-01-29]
Reports/Poster Template/INN_Topology.png

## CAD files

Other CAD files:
Reports/Poster Template/Images/INN_Topology.dwg

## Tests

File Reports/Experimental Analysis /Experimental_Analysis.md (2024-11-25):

#  Experimental Analysis Report

## Introduction
The purpose of this report is to evaluate the application of design constraints through various experimental testing procedures. These results will then be compared against their corresponding measure of success in order to prove effective implementation. For results failing to satisfy requirements, future steps will be provided in order to satisfy the design.

## Requirements Table
|ID	|Constraint or Specification	|Applicable Subsystem|
|---|---|---|
|1|	VFD shall be able to run on a single-phase power input|	Braking Subsystem|
|2	|VFD’s output current shall be greater than the motor’s full load amperage multiplied by the square root of 3	|Braking Subsystem|
|3	|VFD shall be correctly parameterized to the controlled motor’s ratings	|Braking Subsystem|
|4	|An application shall be put into place to dissipate any regenerated power back into the VFD	|Braking Subsystem|
|5	|An E-stop must be present to fully stop operation upon pressing	|Braking Subsystem|
|6	|All electronics shall be properly enclosed and mounted (VFD, Relays, DAQ, etc.)	|All Subsystems|
|7	|DAQ must be able to read the RPM sensor in increments of 1 RPM	|DAQ subsystem|
|8	|DAQ must be able to read the torque sensor in increments of 0.1 N-m	|DAQ subsystem|
|9	|DAQ must be able to read the maximum RPM of motor	|DAQ subsystem|
|10	|UI must be able to start and stop the drive through the HMI	|User Interface subsystem|
|11	|UI must be able to set the frequency reference of the drive through the HMI	|User Interface subsystem|
|12	|UI must be able to save all time-stamped experimental data (torque, rpm, power, DC bus voltage) to an Excel file	|User Interface Subsystem|
|13	|The throttle shall rotate from the starting position to full throttle based on the analog signal from the user interface	|Throttle Control Subsystem|
|14	|The throttle control shall be able to rotate in 1 km/hr increments	|Throttle Control Subsystem|		

# Results

## Constraint 1 – Single phase power input to VFD
#### Experimental Design
After verification of transformer’s ability to step up 10 V to 20 V, using the oscilloscope and waveform generator, successful power up of the VFD, from a 120V power source, without signaling a undervoltage alarm was monitored. A yes was recorded in the table for each successful start-up.
#### Results
|Trial No.|Result|
|--|---|
|1|Yes|
|2|Yes|
|3|Yes|
|4|Yes|

#### Interpretation of Results
Through this experiment, the implemented transformer correctly stepped up 120V to 240V. This allowed for successful start up of the VFD in each trial. 
#### Conclusion
This constraint was proven to be satisfied.

## Constraint 2 – VFD output current properly derated for single phase usage
This constraint is not traditionally testable; however, correct derating can be proven through the VFD’s and motor’s specs.
#### Motor Specs 


#### VFD Specs


#### Interpretation of Result
Since the controlled motor’s full load amperage times the square root of 3 (1.9*√3 = 3.3) is less than the VFD’s max output current (3.5 A), the VFD is correctly sized for single phase power usage.
#### Conclusion
This constraint was proven to be satisfied.

## Constraint 3 – VFD must be correctly parameterized to the motor’s ratings
#### Experimental Design
After verification of correct wiring between the motor and VFD, Yaskawa Drive Wizard was used to correctly parameterize the drive for the controlled motor. These settings were confirmed through monitoring the current output from the drive at different applied frequencies.
#### Results
Trial 1:
|Frequency (Hz)|	Current (A)|
|--|--|
|10|1.31|
|20|1.32|
|30|1.33|
|40|1.35|
|50|1.36|
|60|1.38|

Trial 2:
|Frequency (Hz)	|Current (A)|
|--|--|
|10|	1.30|
|20	|1.32|
|30	|1.34|
|40	|1.35|
|50|	1.37|
|60	|1.38|

#### Interpretation of Results
These two trials prove that the VFD was correctly parameterized for the controlled motor due to the output current never reaching or exceeding the motors FLA (1.7 A).
#### Conclusion
This constraint was proven to be satisfied.

## Constraint 4 – Regenerated power must be dissipated
This constraint is not yet proven due to system not being mechanically mounted to the testing surface. However, the selected braking resistor is sized to dissipate 400 Watts of the maximum expected 245 Watts. Tests will be conducted, once mounted, to prove this resistor’s ability to dissipate regenerated power by monitoring the DC bus voltage level and the output to the braking resistor.

## Constraint 5 - An E-stop must be functionally present 
#### Experimental Design
Upon verification of correct wiring of the E-stop to the VFD, successful functionality was tested through various attempts to stop the motor. A yes was recorded in the table, under the stop section, for each successful emergency stop. A no was recorded, under the start section, for attempting to start while the E-stop was still latched. 
#### Result

|Trial No.	|Stop|	Start|
|--|--|--|
|1	|Yes|	No|
|2	|Yes	|No|
|3	|Yes	|No|
|4|	Yes	|No|
 
#### Interpretation of Result
Through this experiment, the emergency stop’s functionality was proven to operate correctly.
#### Conclusion
This constraint was proven to be satisfied

## Constraint 6 – Electronics shall be properly enclosed and mounted 
This constraint is not traditionally experimental but was satisfied.

## Constraint 7 – DAQ must be able to read the RPM sensor in increments of 1 RPM
#### Experimental Design:
The objective of this experiment was to demonstrate the USB-6003’s ability to precisely measure RPM from torque sensor.  A test was ran to show the RPM measurements at different recorded times.  A small section of the test is shown below.
#### Results:

|Time (s)|	RPM|
|--|--|
|5.728	|6.687|
|5.749|	7.421|
|5.769	|6.108|
|5.789|	5.022|
|5.813|	5.914|
|5.837|	9.019|
|5.860	|13.818|

#### Interpretation of Results:
In this experiment, we are not only able to prove that the RPM is measured in increments of 1, but that it is able to measure changes smaller than 1, with measurements precise to the thousandths place.
#### Conclusion:
This constraint was proven to be satisfied.

## Constraint 8 – DAQ must be able to read the torque sensor in increments of 0.1 N-m 
#### Experimental Design:
This experiment aimed to test and confirm the DAQ’s precision by measuring torque from the torque sensor.  The table shown below displays the torque values during a small sample of the test.
#### Results:

|Time (s)	|Torque (N-m)|
|--|--|
|5.022	|0.826|
|5.045	|0.920|
|5.092	|0.994|
|5.133	|1.065|
|5.155	|1.118|
|5.202	|1.230|
|5.317|	1.303|
	
#### Interpretation of Results:
As seen from the results above, the torque is shown to be going up by less than 0.1 N-m on each measurement. The torque is aleo shown to be measured to the thousandths place, which exceeds the 0.1 N-m increment needed for the constraint.
#### Conclusion:
This constraint was proven to be satisfied.

## Constraint 9 – DAQ must be able to read the maximum RPM of motor
#### Experimental Design:
For this experiment, it is known that the motor is rated for a maximum speed of 1800 RPM.  It is also known that the output signal of the torque sensor is rated for 0-10 V.  This experiment is tested to see if the DAQ can handle the input signal within this voltage range, ensuring that the full signal is accurately measured.
#### Results:


#### Interpretation of Results:
The graph illustrates the RPM range from 0-1800 RPM, with measurements taken at different size increments.  As you can see, the DAQ was able to successfully measure at 1800 RPM.
#### Conclusion:
The constraint was proven to be satisfied. 
	
## Constraint 10 - UI must be able to start and stop the drive through the HMI
#### Experimental Design:
The User-Interface is connected to the start/stop of the drive through a NO relay with the coil connected to a DAQ digital output pin. The output is controlled through a stationary button on the HMI that toggles on each press again.  
The experiment is set up to apply a frequency (0-60 Hz) on the drive, and then the user will press the “start/stop VFD” button and observe the outcome. Once the motor has properly activated, the same “start/stop VFD” button will be pressed, and the outcome will be observed.
#### Results:
|Trial	|Result|
|--|--|
|Start Check 1	|Pass|
|Stop Check 1	|Pass|
|Start Check 2|	Pass|
|Stop Check 2	|Pass|

#### Interpretation of Results:
The HMI start/stop capabilities were thoroughly tested and proved to pass in every scenario. These capabilities are shown to operate correctly in each of the experimental videos in Github.
#### Conclusion:
This constraint was proven to be satisfied.

## Constraint 11 - UI must be able to set the frequency reference of the drive through the HMI
#### Experimental Design	:
The User-Interface is connected to the drive through a DAQ analog pin outputting 0-10 VDC. This voltage controls the frequency of the running motor (0-60 Hz). The experiment is to change to various 0-60 Hz frequencies on the HMI and record the outputs of the motor and drive to verify proper operation.
#### Results:
Set at 5 Hz:

Set at 10 Hz:

Set at 20 Hz:


#### Interpretation of Results
As can be seen in the previous photos and a video on Github, the HMI properly adjusts the frequency reference. The video verifies that the frequency on the HMI is the same as the frequency on the VFD display. This is also verified by the RPM display (on HMI) changing up and down in accordance with the frequency. 
#### Conclusion
This constraint was proven to be satisfied.

## Constraint 12 - UI must be able to save all time-stamped experimental data (torque, rpm, power, DC bus voltage) to a spreadsheet
#### Experimental Design:
The experimental data captured throughout a test run must be captured for later analysis by the user. This is done by saving each desired data point into an array on LabVIEW, and at the end of the run “stop” will be pressed on the HMI. This will prompt the user to save the data to a desired file name and type (.xls). The experiment put into place was to complete a full mock run of the system capturing torque (N-m), speed (RPM), power (W), and DC bus (V). The device tested for this experiment was a battery-operated handheld drill. 
#### Results:


#### Interpretation of Results:
As shown in the table above, all the data captured in the experiment is saved properly to a spreadsheet. The data aligns with the proper elapsed time, so it is time-stamped as the constraint specifies. The entire run of this experiment is displayed in the video on GitHub. 
#### Conclusion:
This constraint was proven to be satisfied.

## Constraint 13 - The throttle shall rotate from the starting position to full throttle based on the analog signal from the user interface
#### Experimental Design:
The throttle control system is operated by a stepper motor, driven by a compact motor driver. The motor driver is controlled by an Arduino microcontroller, which can be programmed to perform various functions depending on what the user needs. For this system, the Arduino was programmed to read in a 0-5V analog signal input and proportionally rotate the stepper motor within a range of 0 to 90 degrees. The rotation is determined by the ratio of the input signal, providing precise and consistent control over the throttle position. To test the results of this several tests were run to ensure that the throttle rotates to the exact angle that it needs to based on the users input.
#### Results:
|Trial	|Result|
|--|--|
|0V	|0°|
|2.5V|	45°|
|5V	|90°|

#### Interpretation of Results:
Although the exact angle of full throttle will change depending on the bike, a 90-degree full throttle was used as a baseline for testing purposes. This full throttle angle can be easily adjusted in the code so that it will suit any bike. However, using the 90-degree throttle for every user input the motor rotated to the correct position.
#### Conclusion:
This constraint was proven to be satisfied.

## Constraint 14- The throttle control shall be able to rotate in 1 km/hr increments
#### Experimental Design:
This constraint ensures that the user will have accurate enough control over the throttle to control it within 1 km/hr increments. This does however depend upon the max speed of the bike being tested. The nema 17 stepper motor that was used has a baseline step angle of 1.8, and since a 90-degree max angle is being used that only gives the user 50 steps within that range. If the bike has a max speed over 50 km/hr or if the max throttle angle is less than 90 degrees, then the user would not be able to control the throttle in 1 km/hr increments.
To fix this a motor driver with a micro stepping was used. This allows the per step angle to be lowered and increases the amount of steps available within the throttles range at the cost of torque. Since throttles require relatively low torque to be rotated this was not an issue.  
#### Results:


#### Interpretation of Results:
This from the datasheet of the A4988 motor driver that was used. It shows the step angle ratio and what pins to set high to achieve it. If it was set to ¼ it would change the per step angle to 0.45 and give the user 200 steps within the 90-degree range which is more than enough steps to control the throttle in 1 km/hr increments.
#### Conclusion:
This constraint was proven to be satisfied.

# Conclusion
|ID|	Constraint or Specification|	Constraint Met?|
|---|---|---|
|1	|VFD shall be able to run on a single-phase power input|	Yes
|2|	VFD’s output current shall be greater than the motor’s full load amperage multiplied by the square root of 3|	Yes|
|3	|VFD shall be correctly parameterized to the controlled motor’s ratings|	Yes|
|4	|An application shall be put into place to dissipate any regenerated power back into the VFD|	N/A|
|5	|An E-stop must be present to fully stop operation upon pressing	|Yes|
|6	|All electronics shall be properly enclosed and mounted (VFD, Relays, DAQ, etc.)	|Yes|
|7	|DAQ must be able to read the RPM sensor in increments of 1 RPM	|Yes|
|8	|DAQ must be able to read the torque sensor in increments of 0.1 N-m	|Yes|
|9	|DAQ must be able to read the maximum RPM of motor|	Yes|
|10	|UI must be able to start and stop the drive through the HMI	|Yes|
|11	|UI must be able to set the frequency reference of the drive through the HMI	|Yes|
|12	|UI must be able to save all time-stamped experimental data (torque, rpm, power, DC bus voltage) to a spreadsheet|	Yes|
|13	|The throttle shall rotate from the starting position to full throttle based on the analog signal from the user interface	|Yes|
|14	|The throttle control shall be able to rotate in 1 km/hr increments	|Yes|

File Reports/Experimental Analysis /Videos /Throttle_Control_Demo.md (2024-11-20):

Video Link for Throttle_Control_Demo:
https://youtu.be/5AOsT5jcX3I

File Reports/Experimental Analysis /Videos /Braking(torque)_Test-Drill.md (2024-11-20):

Video Link for Braking(torque)_Test-Drill: 
https://youtu.be/LPrItjKUE0Y

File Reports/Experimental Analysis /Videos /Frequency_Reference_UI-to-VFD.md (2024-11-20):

Video Link for Frequency_Reference_UI-to-VFD:
https://youtube.com/shorts/aZzF3-TI6N8?feature=share

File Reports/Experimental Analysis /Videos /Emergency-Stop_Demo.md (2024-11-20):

Video Link for Emergency-Stop_Demo:
https://youtu.be/_PjDbi1y1j8

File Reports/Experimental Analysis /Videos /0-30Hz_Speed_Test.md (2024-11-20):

Video Link for 0-30Hz_Speed_Test: 
https://youtu.be/wSG9aRAlblk

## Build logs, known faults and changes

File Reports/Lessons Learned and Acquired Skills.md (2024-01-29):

# Lessons Learned

This document should have a section for each team member. Each engineer should respond to these:

- Reflect on the project, both technical and organizational. What went well? What didn’t go well? 
- What unanticipated problems occurred? 
- What would you do differently if you were to do it over again? 
- What “best practices” have you identified? 
- What words of wisdom would you pass on to future students?
- What new knowledge or skills did you acquire throughout capstone.

Create a subsection addressing each of the above questions in your section of the document.

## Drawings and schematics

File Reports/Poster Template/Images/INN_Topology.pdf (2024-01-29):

## Interneuron ANN Principle Cell ANN

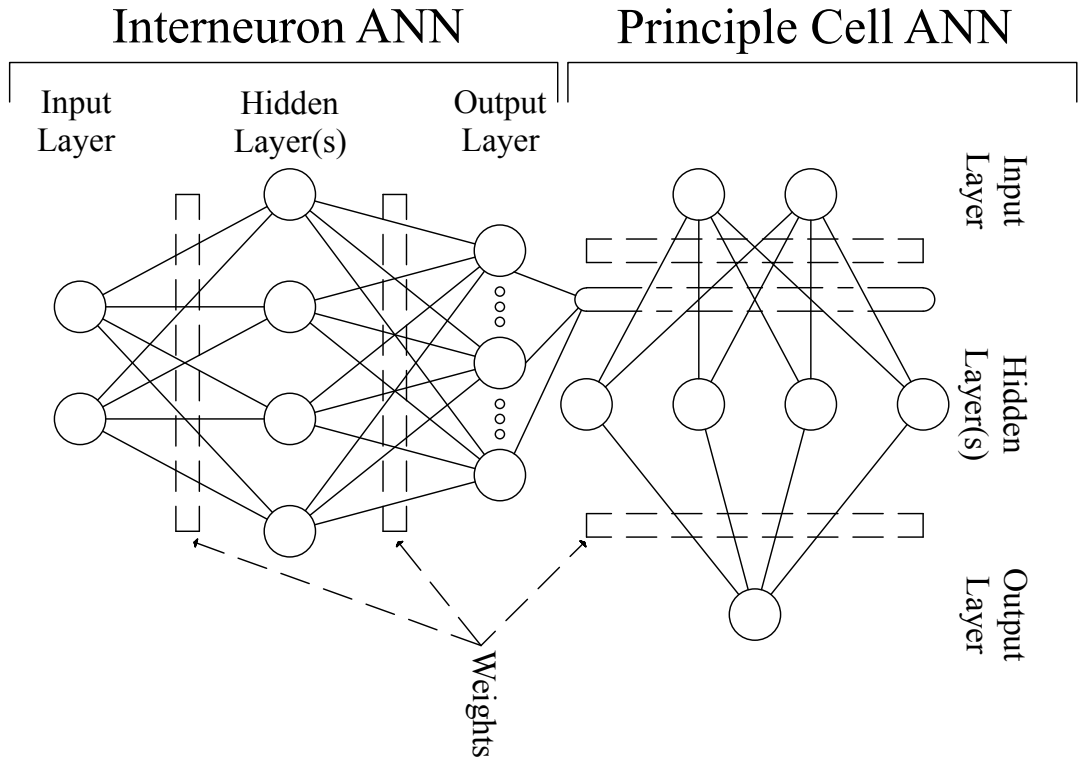
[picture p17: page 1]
Layer; Input; Layer(s); Hidden; Output; Weights; Input Layer; Hidden Layer(s); Output Layer

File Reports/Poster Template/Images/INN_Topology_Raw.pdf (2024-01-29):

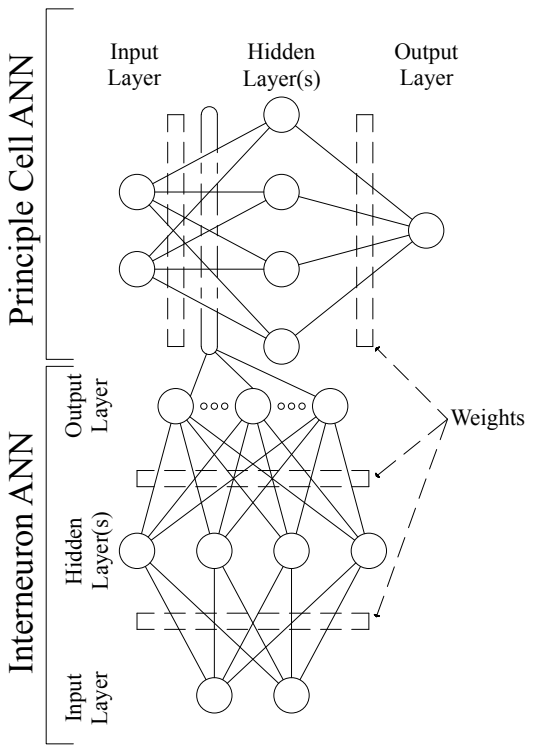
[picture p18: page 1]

Principle Cell ANN Interneuron ANN

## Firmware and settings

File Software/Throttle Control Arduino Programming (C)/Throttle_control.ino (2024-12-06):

#include <AccelStepper.h>
 
// Define the stepper motor and the pins that are connected to
AccelStepper stepper1(1, 2, 5); // 1 means a driver with 2 pins: STEP, DIR. Pins 2 and 5 are for STEP and DIR respectively.
 
// Constants
const int analogPin = A0;                // Analog pin for the 0-5V signal input
const int stepsPerRevolution = 90 / 1.8; // Steps for a full 90-degree throttle rotation
const float maxVoltage = 5.0;            // Maximum input voltage
const int maxDegrees = 90;               // Maximum throttle position in degrees
 
void setup() {
  Serial.begin(9600);
  stepper1.setMaxSpeed(500);       // Set max speed
  stepper1.setAcceleration(1000);  // Set acceleration
  stepper1.setCurrentPosition(0);  // Set the current position to 0
}
 
void loop() {
  // Read the analog value (0-1023) from the analog pin
  int analogValue = analogRead(analogPin);
 
  // Convert analog reading to voltage
  float voltage = analogValue * (maxVoltage / 1023.0);
 
  // Map the voltage to throttle position in degrees (0-90 degrees)
  int targetDegrees = (voltage / maxVoltage) * maxDegrees;
 
  // Convert degrees to steps for the stepper motor
  int targetSteps = (targetDegrees / (float)maxDegrees) * stepsPerRevolution;
 
  // Move the stepper motor to the target position
  stepper1.moveTo(targetSteps);
  while (stepper1.distanceToGo() != 0) {
    stepper1.run();
  }
 
  // Debugging information
  Serial.print("Voltage: ");
  Serial.print(voltage);
  Serial.print(" V, Target Degrees: ");
  Serial.print(targetDegrees);
  Serial.print("°, Target Steps: ");
  Serial.println(targetSteps);
 
  delay(100); // Small delay to avoid excessive updates
}

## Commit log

2024-04-08 Create Throttle Control Detail Design.md
2024-04-11 Sensor-Signoff.md
    Good faith effort (day zero as discussed)
2024-04-11 Revert "Sensor-Signoff.md" (#9)
2024-04-16 Update Throttle Control Detail Design.md
2024-05-03 Create Power Supply.md
2024-09-04 Update Create DAQ Subsystem.md
    Update to constraint 3.
    The reason for the need of a minimum 10 analog inputs was a suggestion from Jesse, as we originally thought we would need more than 2 inputs. The constraint has been updated
    The reason that we have decided to use the USB-6215, compared to other products such as the USB-6003, is due to the fact that it has 4 PWM Outputs, which will be needed in other subsystems. This prod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
2024-09-16 Power Supply.md
    Updated Power Supply Detail Design.
2024-09-16 Update Power Supply.md
    Added manufacturer to BOM
2024-09-16 Update Power Supply.md
    Changed formatting to look cleaner, updated BOM
2024-09-16 Update Power Supply.md
    Added better Arduino Nano pinout diagram
2024-09-18 Update Power Supply.md
2024-12-01 Create Electric Motor Dynamometer Poster.pdf
